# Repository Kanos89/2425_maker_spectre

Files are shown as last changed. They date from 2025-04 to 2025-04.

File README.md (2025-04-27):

# 2425_maker_spectre

## Introduction

### Context

This project is made in the context of the second year option called "Maker" at the French graduate school ENSEA ([https://www.ensea.fr](https://www.ensea.fr)). This option encourages learning by doing, using several manufacturing tools as part of a personal project.

### My project

The idea is to build a drone from almost non-existent knowledge in this field (and so to learn how it's done). The drone will be a quadrotor and its theme will be the spectrum of the Destiny video game series (see photo below). The ultimate aim is to turn it into a companion that will follow its ‘master’ wherever he goes.

Spectrum Drone

## -Project milestones

### -Creating a flight control PCB

### -Creating a light 3D body which represents the drone from the game

### -Creating a 4 in 1 ESC PCB

### -Learn how to implement/use Betaflight for the software part

### -Design and aesthetics

Build a drone inspired by the Spectrum companion from Destiny, keeping the design functional and yet recognizable.

- Use 3D CAD tools to make the drone's skeleton
- (Use of fabrics to lighten the body, maybe in future versions)
- The design shouldn't disrupt the functioning

### For later work - Implement autonomous navigation

Program the drone to follow a "master".

- Compare and decide which technology to use to implement this function by comparing many factors (need for computing power, ease of implementation, precision)

## Tools and Materials

### Tools

#### Software:

- CAD software:
  - We will learn and use Onshape for designing the frame
  - We will design our PCB on KiCAD
- Flight control software:
  - We will use Betaflight solutions

#### Hardware:

- 3D printer for the frame (PCB, motors, and battery support + design of the drone body)
- Fabrics for the design (flat surfaces)
- Soldering station for assembling components on the PCB

### Materials:

#### Actuator

- Brushless motors and propellers suitable for quadrotor drones

#### Control

- Flight controller
- ESC (Electronic Speed Controllers)
  - Designing one can be an objective, buying one is too easy :)

#### Energy

- Use of Lipo 2S for the drone

#### Sensors

- IMU = Accelerometer + Gyroscope
- Barometer for altitude
- For autonomous part (in further versions):
  - Bluetooth antenna (find target relative position)
  - ToF sensor (obstacle avoidance)

#### Communication

- Radio transmitter
- For autonomous part: Bluetooth

#### Frame

- Lightweight materials for the body:
  - PLA: find balance between solidity and weight
  - (Fabric instead of full printed faces)
  - 3D design of the drone with Onshape

Frame Design 1
Frame Design 2
Frame Design 3

- Work done from now on:
  - Flight control PCB with KiCad:

PCB 1
PCB 2
PCB 3

- Honorable mention for KiCad who only crashed 4 times during the rooting phase :)

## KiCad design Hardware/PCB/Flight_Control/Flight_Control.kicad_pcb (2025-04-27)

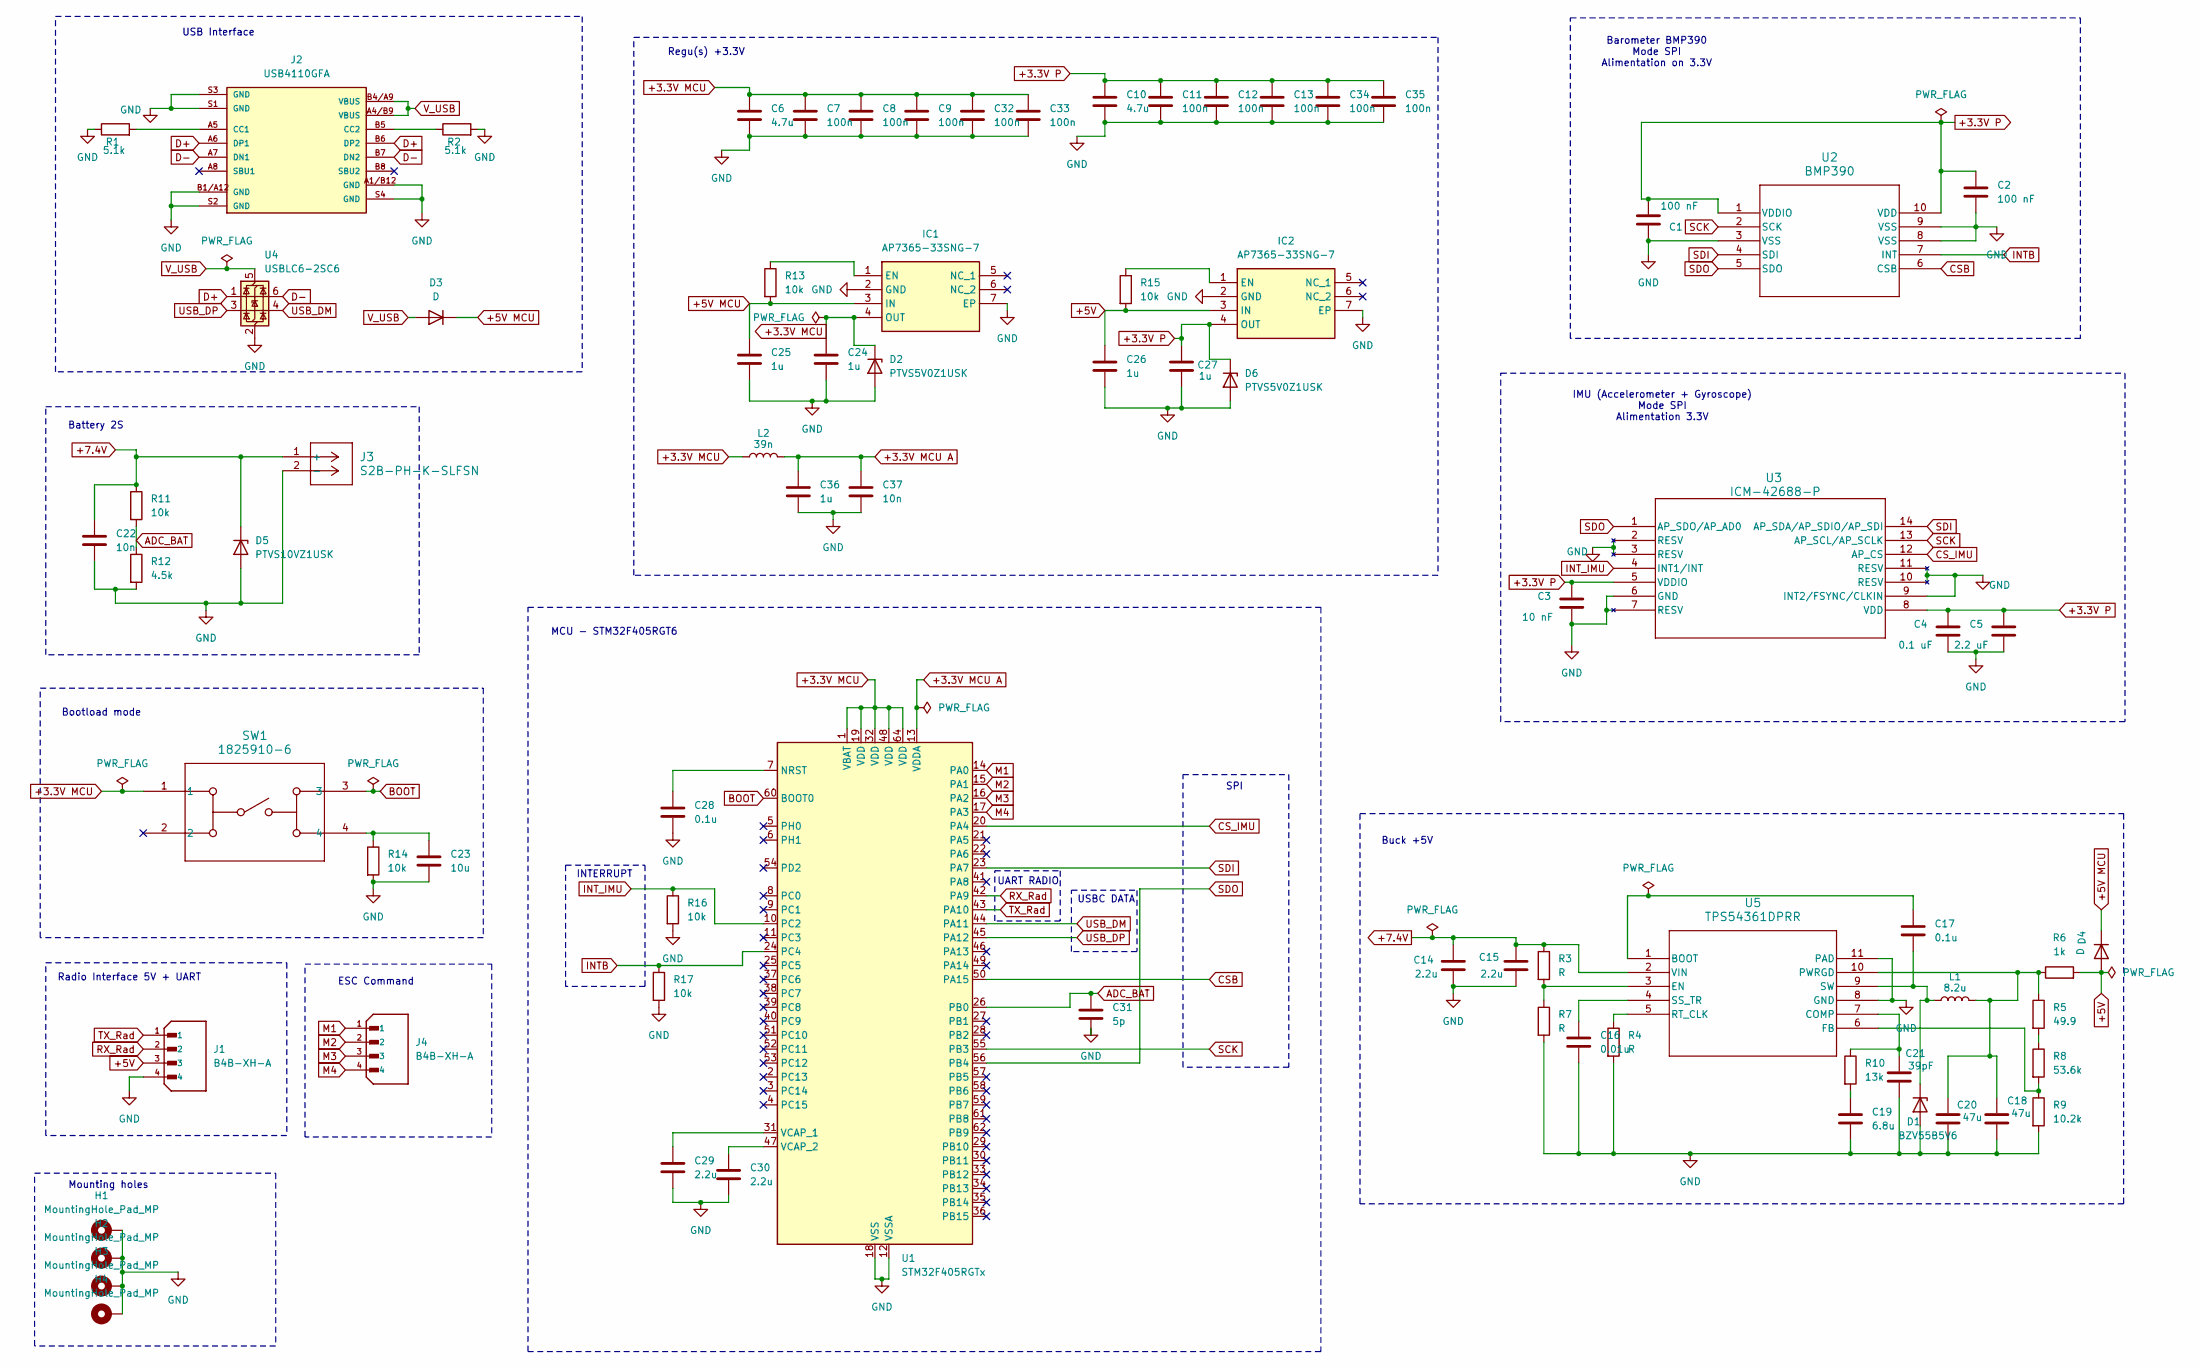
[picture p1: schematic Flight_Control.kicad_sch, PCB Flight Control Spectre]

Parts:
C1, C2: 100 nF; C_0402_1005Metric
C3: 10 nF; C_0402_1005Metric
C4: 0.1 uF; C_0402_1005Metric
C5: 2.2 uF; C_0402_1005Metric
C6, C10: 4.7u; C_0402_1005Metric
C7, C8, C9, C11, C12, C13, C32, C33, C34, C35: 100n; C_0402_1005Metric
C14, C15, C29, C30: 2.2u; C_0402_1005Metric
C16: 0.01u; C_0402_1005Metric
C17, C28: 0.1u; C_0402_1005Metric
C18, C20: 47u; C_0402_1005Metric
C19: 6.8u; C_0402_1005Metric
C21: 39pF; C_0402_1005Metric
C22, C37: 10n; C_0402_1005Metric
C23: 10u; C_0402_1005Metric
C24, C25, C26, C27, C36: 1u; C_0402_1005Metric
C31: 5p; C_0402_1005Metric
D1: BZV55B5V6; D_MiniMELF
D2, D6: PTVS5V0Z1USK; Nexperia_DSN1608-2_1.6x0.8mm
D3, D4: D; D_0402_1005Metric
D5: PTVS10VZ1USK; Nexperia_DSN1608-2_1.6x0.8mm
H1, H2, H3, H4: MountingHole_Pad_MP; MountingHole_2.2mm_M2
IC1, IC2: AP7365-33SNG-7; AP2301SN7; Mouser Part Number 621-AP7365-33SNG-7
J1, J4: B4B-XH-A; JST_B4B-XH-A
J2: USB4110GFA; GCT_USB4110GFA
J3: S2B-PH-K-SLFSN; CONN_S2B-PH-K-S_JST
L1: 8.2u; L_0402_1005Metric
L2: 39n; L_0402_1005Metric
R1, R2: 5.1k; R_0402_1005Metric
R3, R4, R7: R; R_0402_1005Metric
R5: 49.9; R_0402_1005Metric
R6: 1k; R_0402_1005Metric
R8: 53.6k; R_0402_1005Metric
R9: 10.2k; R_0402_1005Metric
R10: 13k; R_0402_1005Metric
R11, R13, R14, R15, R16, R17: 10k; R_0402_1005Metric
R12: 4.5k; R_0402_1005Metric
SW1: 1825910-6; SW4_1825910-B_TEC
U1: STM32F405RGTx; LQFP-64_10x10mm_P0.5mm
U2: BMP390
U3: ICM-42688-P; LGA14_2P5X3X0P91_TDK
U4: USBLC6-2SC6; SOT-23-6
U5: TPS54361DPRR; DPR0010A_TEX

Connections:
+3.3V MCU: C6.1, C7.1, C8.1, C9.1, C24.1, C32.1, C33.1, D2.1 (K), IC1.4 (OUT), L2.1, SW1.1, U1.1 (VBAT), U1.19 (VDD), U1.32 (VDD), U1.48 (VDD), U1.64 (VDD)
+3.3V MCU A: C36.1, C37.1, L2.2, U1.13 (VDDA)
+3.3V P: C1.2, C2.1, C3.1, C4.1, C5.1, C10.1, C11.1, C12.1, C13.1, C27.1, C34.1, C35.1, D6.1 (K), IC2.4 (OUT), U2.1 (VDDIO), U2.10 (VDD), U3.5 (VDDIO), U3.8 (VDD)
+5V: C26.1, D4.2 (A), IC2.3 (IN), J1.3, R6.2, R15.2
+5V MCU: C25.1, D3.1 (K), D4.1 (K), IC1.3 (IN), R13.2
+7.4V: C14.1, C15.1, C22.1, D5.1 (K), J3.1 (+), R3.1, R11.1, U5.2 (VIN)
ADC_BAT: C31.1, R11.2, R12.1, U1.26 (PB0)
BOOT: SW1.3, U1.60 (BOOT0)
CSB: U1.50 (PA15), U2.6 (CSB)
CS_IMU: U1.20 (PA4), U3.12 (AP_CS)
D+: J2.A6 (DP1), J2.B6 (DP2), U4.1 (I/O1)
D-: J2.A7 (DN1), J2.B7 (DN2), U4.6 (I/O1)
GND: C1.1, C2.2, C3.2, C4.2, C5.2, C6.2, C7.2, C8.2, C9.2, C10.2, C11.2, C12.2, C13.2, C14.2, C15.2, C16.2, C18.2, C19.2, C20.2, C21.2, C22.2, C23.2, C24.2, C25.2, C26.2, C27.2, C28.2, C29.2, C30.2, C31.2, C32.2, C33.2, C34.2, C35.2, C36.2, C37.2, D1.2 (A), D2.2 (A), D5.2 (A), D6.2 (A), H1.MP, H2.MP, H3.MP, H4.MP, IC1.2 (GND), IC1.7 (EP), IC2.2 (GND), IC2.7 (EP), J1.4, J2.A1/B12 (GND), J2.B1/A12 (GND), J2.S1 (GND), J2.S2 (GND), J2.S3 (GND), J2.S4 (GND), J3.2 (-), R1.1, R2.2, R4.2, R7.2, R9.2, R12.2, R14.2, R16.2, R17.2, U1.12 (VSSA), U1.18 (VSS), U1.63 (VSS), U2.3 (VSS), U2.8 (VSS), U2.9 (VSS), U3.2 (RESV), U3.3 (RESV), U3.6 (GND), U3.7 (RESV), U3.9 (INT2/FSYNC/CLKIN), U3.10 (RESV), U3.11 (RESV), U4.2 (GND), U5.8 (GND), U5.11 (PAD)
INTB: R17.1, U1.24 (PC4), U2.7 (INT)
INT_IMU: R16.1, U1.10 (PC2), U3.4 (INT1/INT)
M1: J4.1, U1.14 (PA0)
M2: J4.2, U1.15 (PA1)
M3: J4.3, U1.16 (PA2)
M4: J4.4, U1.17 (PA3)
unnamed: C19.1, R10.2
unnamed: C23.1, R14.1, SW1.4
unnamed: C17.2, D1.1 (K), L1.1, U5.9 (SW)
unnamed: IC1.1 (EN), R13.1
unnamed: IC2.1 (EN), R15.1
unnamed: J2.A5 (CC1), R1.2
unnamed: J2.B5 (CC2), R2.1
unnamed: R5.2, R8.1
unnamed: C28.1, U1.7 (NRST)
unnamed: C29.1, U1.31 (VCAP_1)
unnamed: C30.1, U1.47 (VCAP_2)
unnamed: C17.1, U5.1 (BOOT)
unnamed: C21.1, R10.1, U5.7 (COMP)
unnamed: R3.2, R7.1, U5.3 (EN)
unnamed: R8.2, R9.1, U5.6 (FB)
unnamed: C18.1, C20.1, L1.2, R5.1, R6.1, U5.10 (PWRGD)
unnamed: R4.1, U5.5 (RT_CLK)
unnamed: C16.1, U5.4 (SS_TR)
RX_Rad: J1.2, U1.42 (PA9)
SCK: U1.55 (PB3), U2.2 (SCK), U3.13 (AP_SCL/AP_SCLK)
SDI: U1.23 (PA7), U2.4 (SDI), U3.14 (AP_SDA/AP_SDIO/AP_SDI)
SDO: U1.56 (PB4), U2.5 (SDO), U3.1 (AP_SDO/AP_AD0)
TX_Rad: J1.1, U1.43 (PA10)
USB_DM: U1.44 (PA11), U4.4 (I/O2)
USB_DP: U1.45 (PA12), U4.3 (I/O2)
V_USB: D3.2 (A), J2.A4/B9 (VBUS), J2.B4/A9 (VBUS), U4.5 (VBUS)

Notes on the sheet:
Bootload mode
ESC Command
Barometer BMP390 Mode SPI Alimentation on 3.3V
Regu(s) +3.3V
IMU (Accelerometer + Gyroscope) Mode SPI Alimentation 3.3V
SPI
INTERRUPT
Battery 2S
MCU - STM32F405RGT6
Buck +5V
UART RADIO
USB Interface
USBC DATA
Mounting holes
Radio Interface 5V + UART

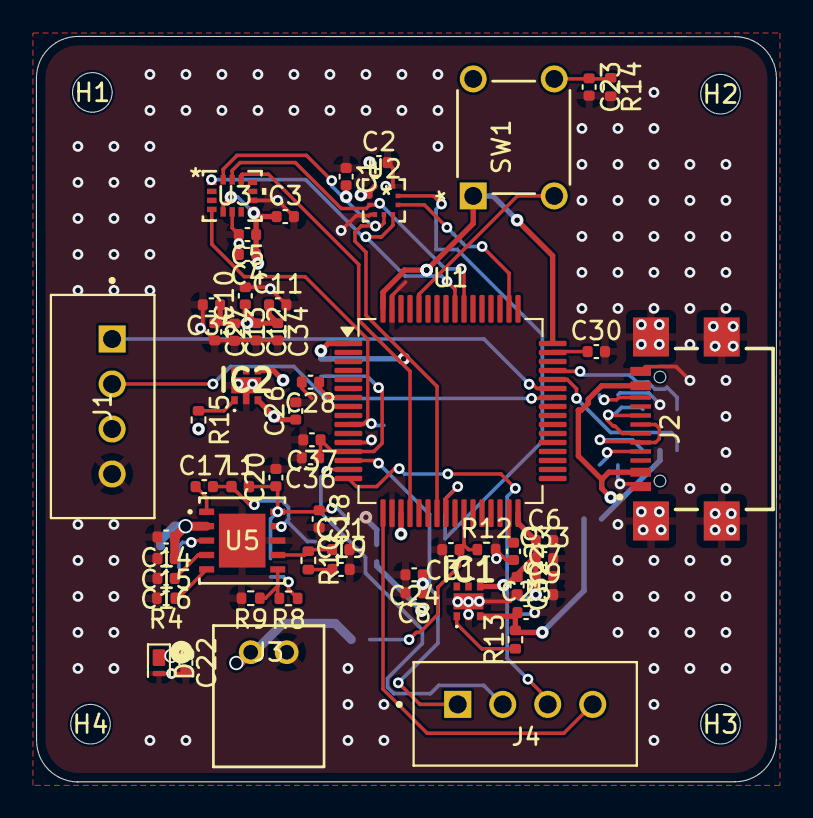
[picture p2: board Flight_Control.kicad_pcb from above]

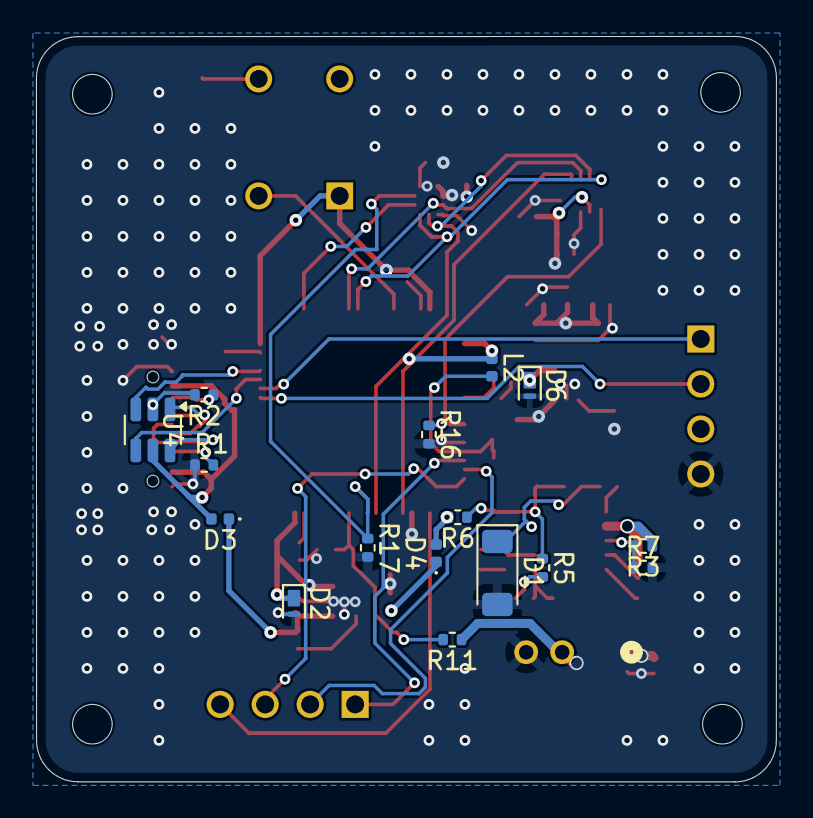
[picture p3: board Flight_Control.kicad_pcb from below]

Board: 4 copper layers, 41.1 x 41.4 mm, 78 parts (16 on the bottom side), 45 nets.

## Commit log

2025-01-20 Main struct of README.md
    Intro + Objectives + idead of Tools and material
2025-03-23 update_pcb + datasheet
    [Flight_Control.kicad_pcb, Flight_Control.kicad_sch]
2025-04-27 add 3D_model
    [Flight_Control.kicad_pcb, Flight_Control.kicad_sch]
